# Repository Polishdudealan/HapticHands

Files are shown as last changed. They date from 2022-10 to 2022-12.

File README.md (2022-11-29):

# Haptic Hands

## Components Specs and Technicalities

### Servo MG90S 5V
Servo in controlled by pwm signals generated by timer 2. System clock is 16 Mhz.
Timer is prescaled by 4. To achieve a period of 20ms necessary for servo control, the counter period is 80,000. 
While the MG90S spec sheet states duty cycle of 1-2ms controls 0-180 degrees, this is not the case for the servos we have.
Our servos take between 0.5-2.5ms to move 0-180 degrees.

### Potentiometer 3.3V
The potentiometer value is access through an ADC port on the nucleo. DMA conversions are maintained by Timer 3 at a frequency of 1kHz.
The value is transferred to the program during the callback. Then is is sampled by user programs.

### Recalibration Button (Currently Blue Button on Nucleo)
DO NOT PRESS WHILE GLOVE IS ON.
This will bring the servo to angle 0 and send command '0' to the PC to map servo angle 0 to potentiometer values.
Then it will bring the servo to angle 180 and send command 'M' to the PC to map servo angle 180 to potentiometer values.
It is the job of the PC to do the rest of the math there (might change in future).
It is unknown if angle 180 would bend a user's fingers too far. It might be better to use a different value

## Unity Package Installation Guideline
1. Install Unity
1. Visit [Unity online asset store](https://assetstore.unity.com/packages/tools/integration/oculus-integration-82022) and add Oculus Integration to your resources. Remember to use the same account to login the Unity and the Unity asset store.
2. Create an empty Unity 3D project
3. In menu bar, go to windows -> package manager. In a drop down menu, find my assets. Then select Oculus Integration, download and import it.
4. Keep the project opening, in local file explorer, find the Unity package for the hand project then double click it.
5. Import all files in the package. (You don't need to select Oculus folder if there is any in the package)(If there is an error showing up, re-import the Oculus Integration)
6. If there are some warning complaining about SerialPort, in menu bar, go to edit -> project settings -> player -> other settings, find .Net settings. Set it to .Net4.0 or some other versions you have, just not set it to .Net2.0.
7. You can adjust the values and properties in the side panels. For gameobject CommManager, you can adjust comport and calibration. You can find scripts in the file explorer on the bottom.

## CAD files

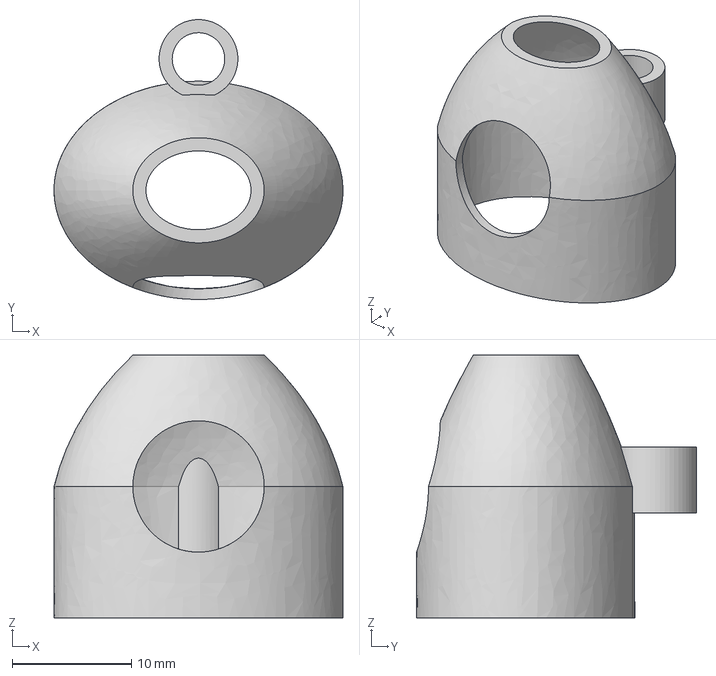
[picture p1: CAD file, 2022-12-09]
CAD/MiddleTip.step
24.2 x 23.4 x 22.0 mm

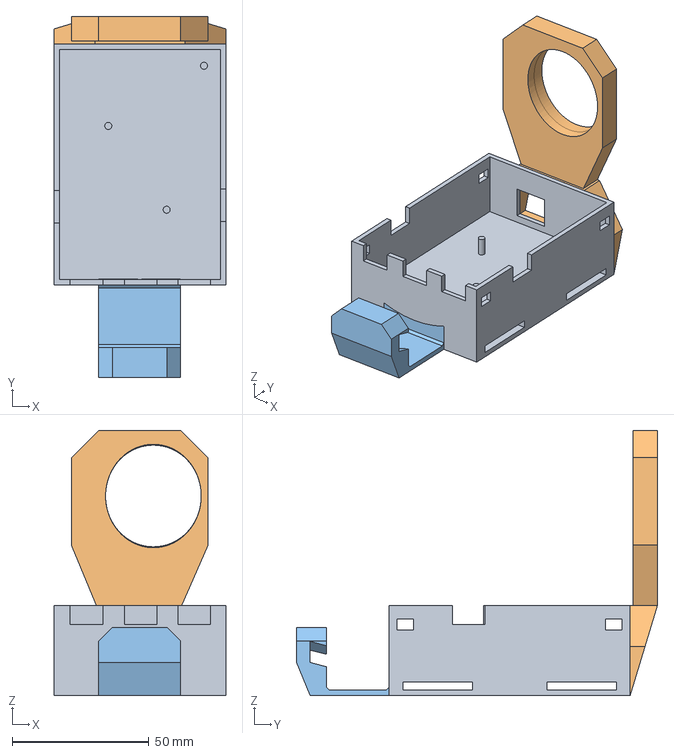
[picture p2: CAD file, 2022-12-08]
CAD/Controller_and_PCB_Mount.step
62.8 x 132.0 x 97.0 mm

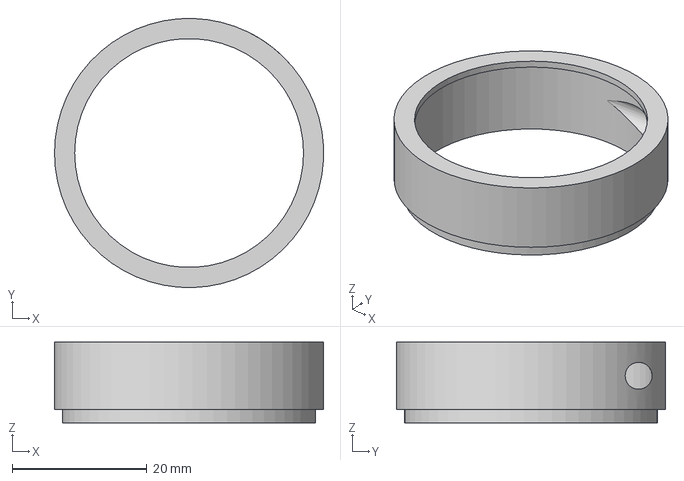
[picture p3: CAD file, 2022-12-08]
CAD/SpoolCover.step
40.0 x 40.0 x 12.0 mm

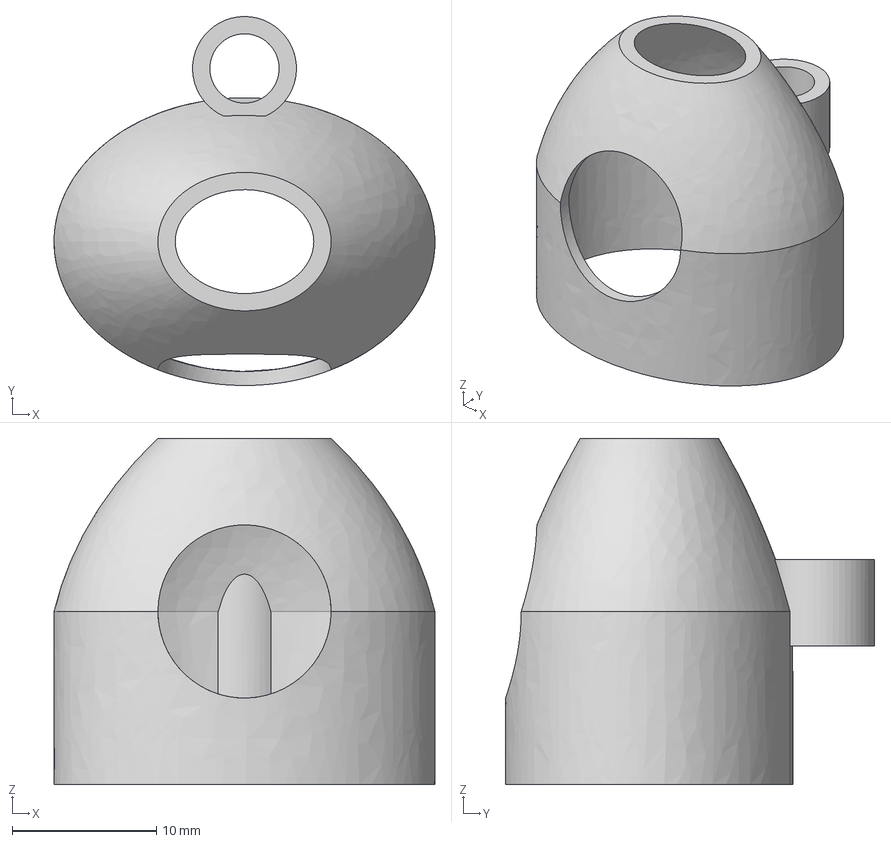
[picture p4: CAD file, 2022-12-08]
CAD/ThumbTip.step
26.4 x 25.6 x 24.0 mm

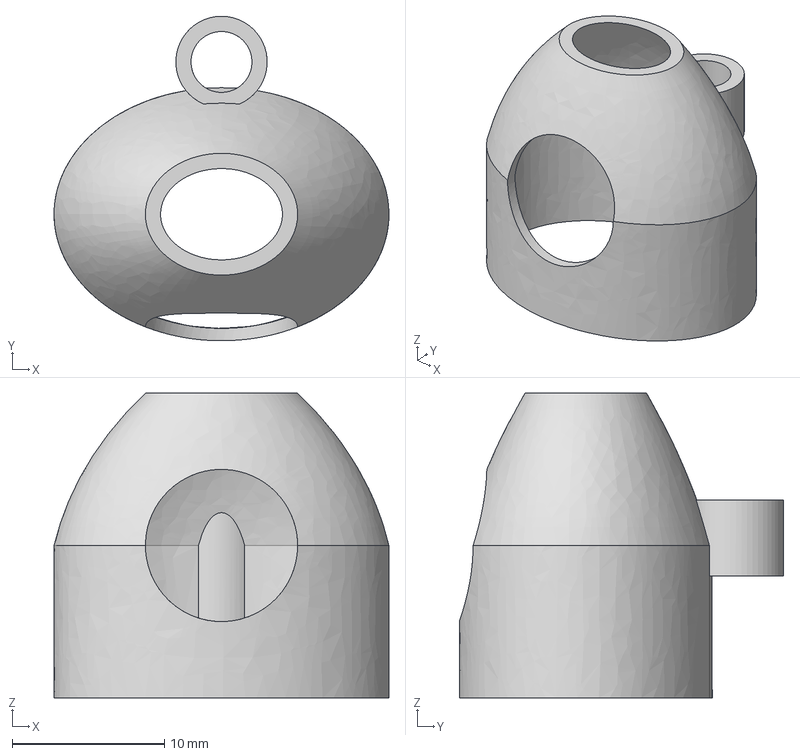
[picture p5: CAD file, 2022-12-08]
CAD/RegularTip.step
22.0 x 21.3 x 20.0 mm

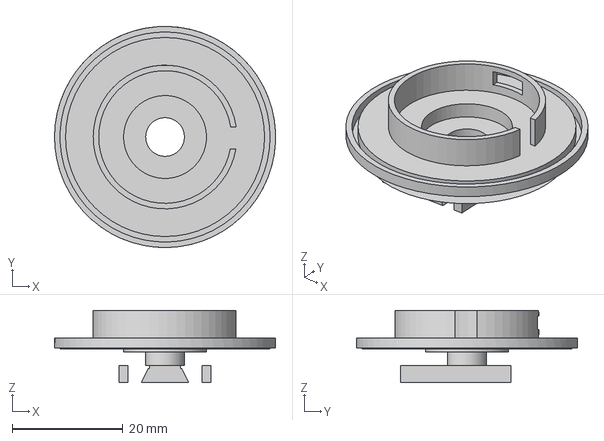
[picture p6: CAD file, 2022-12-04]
CAD/SpringHolder.step
40.0 x 40.0 x 13.1 mm

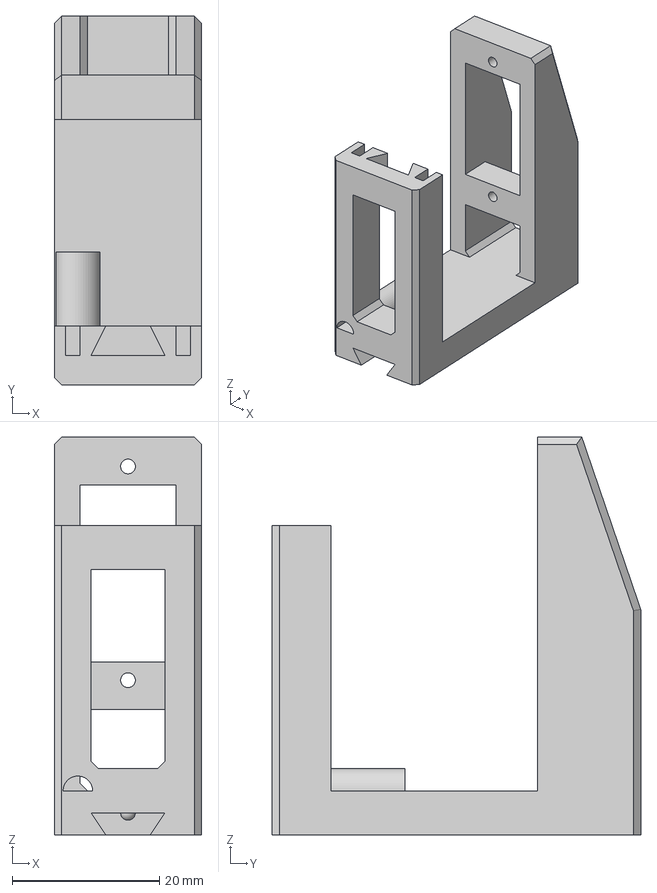
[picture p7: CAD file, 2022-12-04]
CAD/Haptic Module.step
20.0 x 50.0 x 54.0 mm

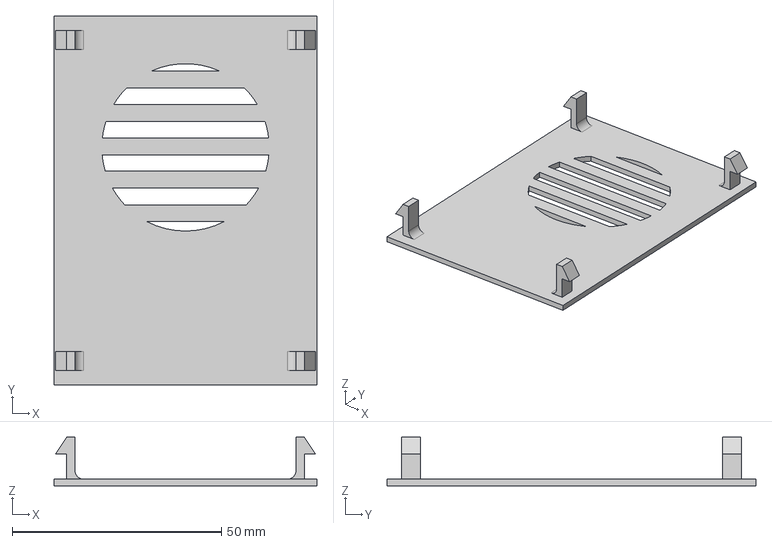
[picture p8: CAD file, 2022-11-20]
CAD/PCB_Lid.step
62.8 x 88.2 x 11.6 mm

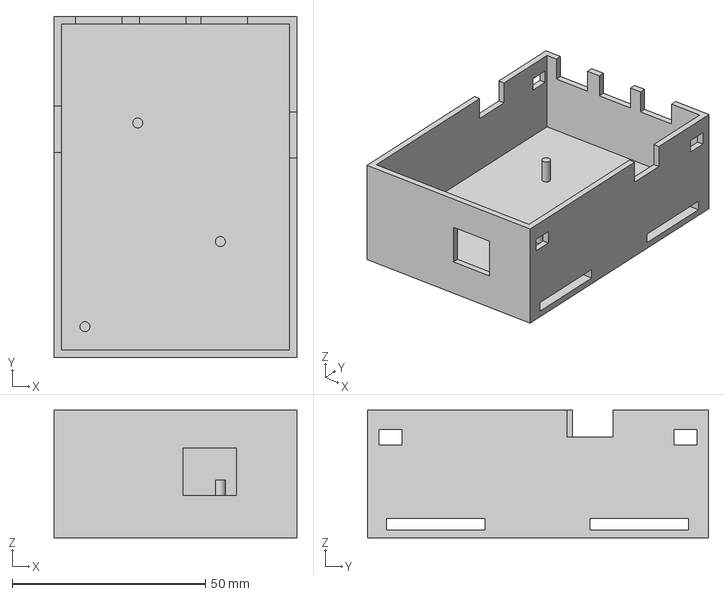
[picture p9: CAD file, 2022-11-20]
CAD/PCB_Mount.step
62.8 x 88.2 x 33.0 mm

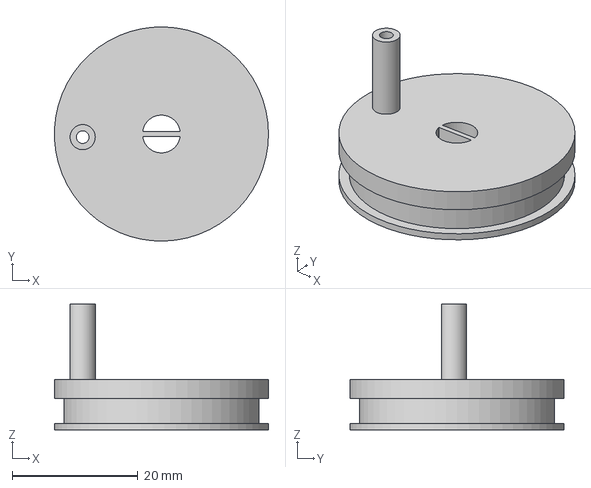
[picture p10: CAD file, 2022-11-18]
CAD/StringHolder.step
34.0 x 34.0 x 20.0 mm

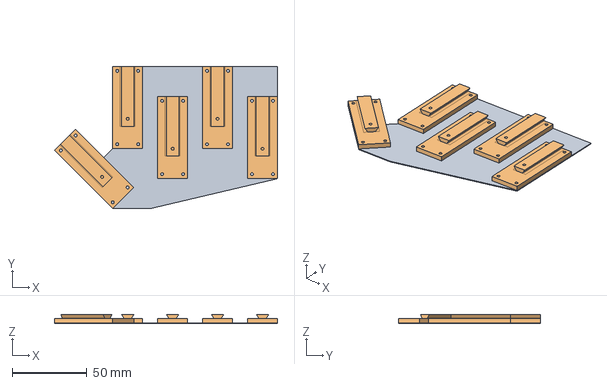
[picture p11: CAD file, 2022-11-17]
CAD/Hand Cover.step
148.9 x 95.0 x 6.30 mm

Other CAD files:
CAD/Haptic_Hands_v28.f3d

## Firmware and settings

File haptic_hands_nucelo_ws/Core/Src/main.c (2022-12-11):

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
/* Includes ------------------------------------------------------------------*/
#include "main.h"

/* USER CODE BEGIN Includes */
#include "potentiometer.h"
#include "servo.h"
#include "comms.h"
#include "vibration.h"
#include "median.h"

/* USER CODE END Includes */

/* USER CODE BEGIN PD */
#define UPDATE_TICK 10
#define UPDATE_COMMAND_TICK 50

/* USER CODE END PD */

 ADC_HandleTypeDef hadc1;
DMA_HandleTypeDef hdma_adc1;

TIM_HandleTypeDef htim2;
TIM_HandleTypeDef htim3;
TIM_HandleTypeDef htim4;

UART_HandleTypeDef huart6;
DMA_HandleTypeDef hdma_usart6_rx;

/* USER CODE BEGIN PV */

FingerState finger_state = (FingerState){.valid=0,
										  .angles = {0,0,0,0,0},
										  .collisions = {0,0,0,0,0}
										};

uint8_t calibrate_status = 0;
uint32_t timer3_cnt;
uint16_t pot_readings[NUM_FINGERS];

/* USER CODE END PV */

void SystemClock_Config(void);
static void MX_GPIO_Init(void);
static void MX_DMA_Init(void);
static void MX_ADC1_Init(void);
static void MX_USART6_UART_Init(void);
static void MX_TIM2_Init(void);
static void MX_TIM3_Init(void);
static void MX_TIM4_Init(void);
/* USER CODE BEGIN PFP */
// Checks if a collision has occurred on any of the fingers
void checkCollisions(){
	HAL_GPIO_WritePin(GPIOC, GPIO_PIN_1, finger_state.collisions[1]);
	for(int i = 0; i < NUM_FINGERS; i++){
		if(finger_state.collisions[i] == 1){
			servoSetPosRaw(i, finger_state.angles[i]);
			vibrationOnForDuration(i, 20);
		}
		else{
			uint16_t p = potRead(i);
			servoSetPosRaw(i, p);
			resetVibration(i);
		}
	}
  }

void update_command() {
	// Send "SOP(wrapped in sendCommand), Command type, [msb, lsb] * 5"
	// sendCommand('1', pot_readings[0], pot_readings[1], pot_readings[2], pot_readings[3], pot_readings[4]);
	//uint16_t test = getMedian(1);
	sendCommand('1', getMedian(0), getMedian(1), getMedian(2), getMedian(3), getMedian(4));
}

  // Main update loop
  // Reads pot value, sends it via uart, moves servo accordingly
void update(){
	 for(int i = 0; i < NUM_FINGERS; i++){
		 pot_readings[i] = potRead(i);
		 updateMedianArray(i, pot_readings[i]);
	 }
	checkCollisions();
	checkVibration();
}
/* USER CODE END PFP */

/* USER CODE BEGIN 0 */

#ifdef DEBUG
void HAL_Delay(uint32_t Delay){
	for(volatile int i = 0; i < Delay * 1000; ++i);
}
#endif

void HAL_GPIO_EXTI_Callback(uint16_t GPIO_PIN){
	if(GPIO_PIN != GPIO_PIN_13) return;
	// Map & calibrate potentiometers with servos on PC
	HAL_Delay(10);
	for(int i = 0; i < NUM_FINGERS; i ++){
		pot_readings[i] = potRead(i % NUM_FINGERS); // Update per finger
	}
	HAL_Delay(10);
	sendCommand(calibrate_status ? CALIBRATEMAX : CALIBRATEZERO, pot_readings[0], pot_readings[1], pot_readings[2], pot_readings[3], pot_readings[4]);
	calibrate_status = !calibrate_status;
}

void HAL_TIM_PeriodElapsedCallback(TIM_HandleTypeDef *htim){
	if(htim == &htim3){
		// increment ms counter
		timer3_cnt = (timer3_cnt + 1) % 51;
	}
}

/* USER CODE END 0 */

/**
  * @brief  The application entry point.
  * @retval int
  */
int main(void)
{
  /* MCU Configuration--------------------------------------------------------*/

  /* Reset of all peripherals, Initializes the Flash interface and the Systick. */
  HAL_Init();

  /* Configure the system clock */
  SystemClock_Config();

  /* Initialize all configured peripherals */
  MX_GPIO_Init();
  MX_DMA_Init();
  MX_ADC1_Init();
  MX_USART6_UART_Init();
  MX_TIM2_Init();
  MX_TIM3_Init();
  MX_TIM4_Init();
  /* USER CODE BEGIN 2 */

  // Start timers(tim2 tim4) for servos
  servoInit();

  // Timer for DMA ADC conversions
  HAL_TIM_Base_Start_IT(&htim3);

  // Start ADC dma
  // Timer 3 starts DMA conversion once per millisecond
  HAL_ADC_Start_DMA(&hadc1, adc_buffer, 5);

  // Starts UART receive interrupts
  UART_INIT();

  // Variable initialization
  for (int i = 0; i < NUM_FINGERS; i++) {
	  servoSetPos(i, 180);
  }

  // Turn on debug LEDs
  //HAL_GPIO_WritePin(GPIOC, GPIO_PIN_1, SET);
  //HAL_GPIO_WritePin(GPIOC, GPIO_PIN_2, SET);

  /* USER CODE END 2 */

  /* Infinite loop */
  /* USER CODE BEGIN WHILE */

  while (1)
  {
	 // Run every update_tick ms
	 if(timer3_cnt % UPDATE_TICK == 0){
		 update();
	 }

	 // Run every update_command_tick ms
	 if(timer3_cnt % UPDATE_COMMAND_TICK == 0){
		 update_command();
	 }

    /* USER CODE END WHILE */

    /* USER CODE BEGIN 3 */
  }
  /* USER CODE END 3 */
}

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


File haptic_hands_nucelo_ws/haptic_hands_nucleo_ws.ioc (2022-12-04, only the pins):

Mcu.UserName=STM32F411RETx
PA1.GPIO_Label=Backup_GPIO_0
PA1.Signal=GPIO_Output
PA10.GPIO_Label=vib2
PA10.Signal=GPIO_Output
PA11.GPIO_Label=vib1
PA11.Signal=GPIO_Output
PA12.GPIO_Label=vib0
PA12.Signal=GPIO_Output
PA13.Signal=SYS_JTMS-SWDIO
PA14.Signal=SYS_JTCK-SWCLK
PA15.GPIO_Label=servo1
PA15.Signal=S_TIM2_CH1_ETR
PA5.GPIO_Label=pot0
PA5.Signal=ADCx_IN5
PA6.GPIO_Label=pot1
PA6.Signal=ADCx_IN6
PA7.GPIO_Label=pot2
PA7.Signal=ADCx_IN7
PA8.GPIO_Label=vib4
PA8.Signal=GPIO_Output
PA9.GPIO_Label=vib3
PA9.Signal=GPIO_Output
PB0.GPIO_Label=pot3
PB0.Signal=ADCx_IN8
PB1.GPIO_Label=pot4
PB1.Signal=ADCx_IN9
PB10.GPIO_Label=servo2
PB10.Signal=S_TIM2_CH3
PB13.Signal=GPIO_Output
PB3.GPIO_Label=servo0
PB3.Signal=S_TIM2_CH2
PB6.GPIO_Label=servo3
PB6.Signal=S_TIM4_CH1
PB7.GPIO_Label=servo4
PB7.Signal=S_TIM4_CH2
PC1.GPIO_Label=Debug_LED_0
PC1.Signal=GPIO_Output
PC13-ANTI_TAMP.Signal=GPXTI13
PC2.GPIO_Label=Debug_LED_1
PC2.Signal=GPIO_Output
PC3.GPIO_Label=Backup_GPIO_1
PC3.Signal=GPIO_Output
PC6.Signal=USART6_TX
PC7.Signal=USART6_RX

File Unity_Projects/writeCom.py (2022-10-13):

from time import sleep
import serial
ser = serial.Serial('COM2', 115200)
ser.flush()
finger_val = [0, 0, 0, 0, 0]
delta = [4, 4, 4, 4, 4]
while True:
    for i in range(5):
        if finger_val[i] > 0x0FFF:
            finger_val[i] = 0
        else:
            finger_val[i] += delta[i]
    print(finger_val)
    finger_str = [
        b''.join(
            [
                ((x >> 8) & 0xFF).to_bytes(1, 'big'), 
                (x & 0xFF).to_bytes(1, 'big')
                ]
            ) for x in finger_val
        ]
    textMsg = bytes("$1", 'utf-8') + b''.join(finger_str)# + bytes("^", 'utf-8')
    print(textMsg)
    ser.write(textMsg)
    sleep(0.01)

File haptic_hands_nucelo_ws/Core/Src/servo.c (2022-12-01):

/*
 * servo.c
 *
 *  Created on: Oct 4, 2022
 *      Author: alan1
 */

#include "comms.h"
#include "servo.h"
#include <stdint.h>

extern TIM_HandleTypeDef htim2;
extern TIM_HandleTypeDef htim4;

// Attaches servo to certain pin
void servoInit(){
	HAL_TIM_PWM_Start(&htim2, TIM_CHANNEL_1);
	HAL_TIM_PWM_Start(&htim2, TIM_CHANNEL_2);
	HAL_TIM_PWM_Start(&htim2, TIM_CHANNEL_3);
	HAL_TIM_PWM_Start(&htim4, TIM_CHANNEL_1);
	HAL_TIM_PWM_Start(&htim4, TIM_CHANNEL_2);
	return;
}

void servoSetVal(uint8_t finger, uint16_t val) {
	switch(finger){
		case 1:
			TIM2->CCR1 = val;
			break;
		case 0:
			TIM2->CCR2 = val;
			break;
		case 2:
			TIM2->CCR3 = val;
			break;
		case 3:
			TIM4->CCR1 = val;
			break;
		case 4:
			TIM4->CCR2 = val;
			break;
		default:
			break;
	}
}

// Sets position of the servo
// Takes in degrees
//
void servoSetPos(uint8_t finger, uint8_t deg){
	// Modification to flip servo direction
//	deg = 180 - deg;
    // 4000 offset because control ranges from 1ms-2ms duty cycle
	// 0.045 is determined by 180 deg / 8000 cnts per millisecond
	// 2 is because 180 deg is mapped across 2 ms, not 1
	// servo seems to be mapped from 2000-10000 => 0-180 deg
	// This is NOT what the spec said
//	TIM2->CCR1 = (uint16_t)(2.0*(deg / 0.045) + 2000);
	// Try this for multi-finger
	uint16_t val = 1000 + (double) 2 * 4000.0 * deg / 180.0;
	servoSetVal(finger, val);
}

/*
 *
 * Write servo position with the raw 2byte value from
 * the potentiometer
 *
 */
void servoSetPosRaw(uint8_t finger, uint16_t deg){
	uint16_t val = 1000 + (double) 2 * 4000.0 * deg / 0x0FFF; //Maybe right shift by 12? reduce FP?
	//uint16_t val = 1000 + (125*deg) >> 6; //TODO test
	//uint16_t val = 1000 + 2 * deg
	servoSetVal(finger, val);
}

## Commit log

2022-10-02 First commit. Uploading first STM code. Includes DMA potentiometer sampling
2022-10-05 Servo, potentiometer and uart tested
2022-10-08 sending and receiving commands. Can control hand with pot and servo can react to collisions with objects.
    [comms.c, haptic_hands_nucelo_ws.ioc, main.c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]
2022-10-11 Added button interrupt for calibration
2022-10-11 Added readme description of button calibration interrupt
2022-10-11 Generalized interrupt for when we add more fingers
2022-10-12 fix-change name of project
    [comms.c, haptic_hands_nucleo_ws.ioc, main.c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]
2022-10-12 dev-add unity project, calibration finished
2022-10-13 Cleared some warnings - why no Pot DMA?
2022-10-13 Fixed DMA for ADC
    [comms.c, haptic_hands_nucleo_ws.ioc, main.c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]
2022-10-13 Cleaned up interrupt
2022-10-14 Restructured finger_state and main. Restructed collision checking. Tested with breadboard and unity setup.
    [comms.c, main.c, servo.c]
2022-10-18 Integration changes for finger. Need to ensure that scaling is consistant (see change in servo.c)
2022-10-19 Milestone 1 Demo code. Fixed position flip in supplementary angle between potentiometer and servo.
    [main.c, servo.c]
2022-10-22 Added support for 5 fingers
2022-10-25 Added beginning eagle schematic
    [haptichandpcb.sch]
2022-10-25 altium files
    [Haptic_hands.PrjPcb, haptic_hands.SchDoc]
2022-10-25 schematic edit
    [haptic_hands.SchDoc]
2022-10-26 Power, gnd connections mostly done
    [haptic_hands.SchDoc]
2022-10-26 headers added. stlink, power left
    [haptic_hands.SchDoc]
2022-10-26 dev-add vibration motor, fix the servo pos mapping, clear up the code a bit.
    [haptic_hands_nucleo_ws.ioc, main.c, main.h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]
2022-10-26 added more headers
    [haptic_hands.SchDoc]
2022-10-27 transistors added
    [haptic_hands.SchDoc]
2022-10-27 Added FTDI and USB port to PCB design - need SW programmer interface
    [Haptic_hands.PrjPcb, PCB1.PcbDoc, PcbLib1.PcbLib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]
2022-10-27 Added actual PCB file
    [Haptic_hands.PrjPcb, haptic_hands.SchDoc]
2022-10-29 dev-reduce redundant code, fix pwm init, change pwm channle order
    [haptic_hands_nucleo_ws.ioc, main.c, main.h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]
2022-10-31 Changed servo3 from pin PA0 to PA2 due to potential conflicts
2022-10-31 added LEDs
    [haptic_hands.SchDoc]
2022-11-01 dev-switch to use timer4, remap the servo functions
2022-11-01 PCB unrouted
    [Haptic_hands.PrjPcb, PCB3.PcbDoc, haptic_hands.PcbDoc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]
2022-11-01 Added backup gpio pins and leds to ioc
2022-11-03 Changes in components, routing left
    [PCB3.PcbDoc, haptic_hands.SchDoc]
2022-11-03 Traces done. Changed to 4-layer board. TODO: add mounting holes
    [Haptic_hands.PrjPcb, PCB3.PcbDoc, haptic_hands.SchDoc]
2022-11-03 Added LDO caps. Added Logo.
    [PCB3.PcbDoc, haptic_hands.SchDoc]
2022-11-04 PCB work 11_03. Nearly complete
    [Haptic_hands.PrjPcb, PCB3.PcbDoc, haptic_hands.SchDoc]
2022-11-04 added labels, re-routed wires a little
    [Haptic_hands.PrjPcb, PCB3.PcbDoc]
2022-11-06 Changed layer height
    [Haptic_hands.PrjPcb, PCB3.PcbDoc]
2022-11-08 Added working pcb files (with correct layers). Added CAD models for components.
    [Haptic_Hands_v28.f3d, Haptic_hands.PrjPcb, PCB3.PcbDoc]
2022-11-08 drill hole changes
    [Haptic_hands.PrjPcb, PCB1.PcbDoc, PCB3.PcbDoc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]
2022-11-09 fix-fix vib, fix servo mapping, fix comm freq
    [main.c, servo.c]
2022-11-10 dev-add median algorithm, fix index in vibration
    [main.c, vibration.c]
2022-11-11 dev-add soft calibration unity package
2022-11-16 Added PCB and PCB mount CAD models.
    [PCB_Mount.step]
2022-11-17 Added strap holes for mounting to PCB mount
    [PCB_Mount.step]
2022-11-17 Added lid to PCB mount. Uploaded some other 3D models
    [Hand Cover.step, Haptic Module.step, PCB_Lid.step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]
2022-11-18 dev-add string holder and modified spring holder
    [SpringHolder.step, StringHolder.step]
2022-11-18 fix-fix spring and string
    [SpringHolder.step, StringHolder.step]
2022-11-18 Updated haptic module component
    [Haptic Module.step]
2022-11-20 Updated springholder and pcb case
    [PCB_Lid.step, PCB_Mount.step, SpringHolder.step]
2022-11-29 Fixed some warnings and code style issues
    [main.c, main.h, potentiometer.c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]
2022-12-01 Fixed servo pwm error. Added code to turn on debug lights
    [haptic_hands_nucleo_ws.ioc, main.c, servo.c]
2022-12-03 fix-add $ polling and fix command send, still have problems: when some collision happens, the collision state sent by unity is correct but the collision state on stm is not updated.
    [comms.c, main.c]
2022-12-04 Modified CAD models
    [Haptic Module.step, SpringHolder.step]
2022-12-04 minor stm changes while debugging collision issue. NOT A FIX
    [comms.c, haptic_hands_nucleo_ws.ioc]
2022-12-08 dev-update unity package and CAD models
    [Controller_and_PCB_Mount.step, RegularTip.step, SpoolCover.step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]
2022-12-08 dev-add device calibration
2022-12-09 Added final expo version of unity program. Added one more CAD model
    [MiddleTip.step]
2022-12-11 dev-fix naming convention of median.h
    [main.c]

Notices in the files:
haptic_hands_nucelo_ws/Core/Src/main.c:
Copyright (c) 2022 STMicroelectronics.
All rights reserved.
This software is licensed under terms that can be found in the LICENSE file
